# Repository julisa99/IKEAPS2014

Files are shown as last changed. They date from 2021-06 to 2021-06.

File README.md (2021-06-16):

# IKEAPS2014
Control your IKEA PS 2014 lamp with a servo motor and Wemos d1 mini (ESP8266) via Alexa – dimmable solution 💡

The year is 2021 and I finally managed to put my Ikea hack online. Of course, there are already countless hacks to be found on the internet. The special thing about this tutorial is that I set myself a goal: easy to replicate, easily replaceable and most importantly, the lamp not only just opens and closes; It is dimmable! You can open the lamp for example 20% or 80% via Alexa.
In the end, I only use the ESP8266 and a servo with an encoder, but more details will follow after the short animation of the working lamp:
<p align="center">

</p>

## Materials
1. [1x IKEA PS 2014 lamp](https://www.ikea.com/de/de/p/ikea-ps-2014-haengeleuchte-weiss-silberfarben-90311494/)
2. [1x WeMos D1 Mini](https://www.amazon.de/dp/B01N9RXGHY)
3. [1x Micro USB cable](https://www.amazon.de/dp/B01A9GLG6Q/)
4. [1x Feetech FB5317M 360° Servo - includes Analog Feedback with Magnetic Encoder](https://www.premium-modellbau.de/feetech-fb5317m-3600-cont-digital-servo-65g-17-5kg-feedback-arduino)
5. [1x servo mount](https://www.amazon.de/dp/B07SGPBCHM)
6. [1x sewing thread spool](https://www.amazon.de/dp/B074HF2KZV/)
7. [1x power supply 5V](https://www.amazon.de/dp/B00MWQD43U/)
8. [2x Wago connection clamp 3 x 0,2-4mm²](https://www.amazon.de/dp/B071ZHC2QH)
9. [2x 10cm braids 1,5mm² thickness for 230V](https://www.amazon.de/dp/B077JZNWV7)
10. [2x jumper cable male](https://www.amazon.de/dp/B01EV70C78/)
11. [1x 30cm 4-wire white cable or 8-wire flat ribbon telephone cable for extension from motor to ceiling](https://www.amazon.de/dp/B07TGKPFHK/)
12. [7x white cable ties](https://www.amazon.de/dp/B07JMKK66N)
13. [Optional: Crimping tool for cable lugs](https://www.amazon.de/gp/product/B07QMHNKW3)
14. [Optional: Crimping tool Dupont Set](https://www.amazon.de/dp/B078K9DT69/)
15. 3D printer for [servoHolder.stl](https://github.com/julisa99/IKEAPS2014/blob/main/servoHolder.stl)

## Preparation
Remove the white plastic spool from the frame of the lamp (see graphic) and cut the cord so that one side of the cord is longer than the other. We will knot the longer side to the sewing thread spool later. You can make the shorter side even shorter, because one cord with ball will be decoration.
<p align="center">

</p>

## Composition
Be careful, check that you have turned off the fuses of your power supply, otherwise you might severely hurt yourself. I know that even without being an electrician ;)
<p align="center">

</p>

As you can see in the graphic, the wiring is not complicated. The orange Wago clamps and the cable lugs provided an easy and comfortable way to set everything up. But now follows a little explanation:

The servo motor has four cables. The orange one (analog feedback) you plug into A0 of the Wemos. The white data cable you plug into D0. I don't supply the power for motor via the microcontroller, because it only gives up to 500mA via the pins, but the motor could overload this, by drawing up to 1800mA when it turns. The power for the motor and microcontroller comes from the power supply, which outputs 5V. To make the four cables fit to the 2 connectors, I feed + and - through each of the Wago clamps and put a jumper cable in there. Then I screwed the respective jumper cables (red: + and black: -) to the power supply by replacing the end with cable lugs.
I then connected the yellow ground cable from the ceiling to the ground of the power supply. Finally I attached cable lugs to two 10cm cables (with 1,5mm² thickness because of the higher current) to attach them at N and L between the power supply and the lamp as shown in the graphic with the brown and blue cable.

I later placed the servo motor in the lamp and put everything else up in the tray on the ceiling. Since the four cables from the motor are too short to reach from the ceiling to the center of the lamp, I used a white flat telephone cable and connected that as a 30cm extension to the cable ends from the motor and then the other end of the telephone cable into the microcontroller/Wago clamps. My telephone cable had 8 wires, where I then attached Dupont connectors myself, so that always 2 wires were together and I thus had 4. Alternatively you can use a 4-wire cable. (I got it as a drum of 100 meters of telephone cables, whose remains I still need to find some good use for. If you are from Germany near Berlin I can give you some :D)

<p align="center">



</p>

That's all for the cabling. Now only the attachment of the sewing thread spool to the motor and then the attachment of the motor in the lamp is missing.
I screwed the sewing thread spool to the black circular servo horn with two small screws and then screwed the servo horn to the motor.
<p align="center">

</p>

I then screwed the motor to the aluminum servo holder I bought and then made my own 3D model [servoHolder.stl](https://github.com/julisa99/IKEAPS2014/blob/main/servoHolder.stl) where I screwed the servo holder to it. My 3D model consists of a rod with two slots at the ends, where a cable tie is attached, which then holds on the frame of the lamp. This makes it easy to remove the motor at any time. 
<p align="center">

</p>

Afterwards you attach the white cord of the lamp to the metal sewing thread spool with a knot. With further cable ties you can lead your cable along the frame up to the ceiling. The assembly is finished!

<p align="center">

</p>

## Arduino IDE and library
In order to control the ESP8266, the following address must be added in the Arduino IDE under `File->Preferences->Additional Board Manager URLs`: http://arduino.esp8266.com/stable/package_esp8266com_index.json. Then you can type "esp8266" in the search field under `Tools->Board->Boards Manager`and click on `Install`. Now the `LOLIN(WEMOS) D1 R1 & mini` appears under the boards and can be selected.

For communication with Alexa I use the library "espalexa" with version 2.4.7. There is a small bug, which is fixed, if in line 197 in Espalexa.h `arg(0)` is changed to `argName(0)`.

In line 5 and 6 of [IKEAPS2014.ino](https://github.com/julisa99/IKEAPS2014/blob/main/IKEAPS2014.ino) you have to enter your access data for your wifi. After that you can upload the code to your microcontroller. In the end you can ask Alexa to search for new devices and you should find the device "star".

## How it works
When you command "Alexa, open star to 20%"; the function `deviceChanged(brightness)` is executed, where the 20% is passed as `brightness` of "51", since brightness value is between 0-255.
Now I calculate how often the sewing thread spool has to rotate. I have set `MAX_ROTATION` to how many times my cord must be wound on the sewing thread spool until the lamp is fully open. In my case, `MAX_ROTATION` is 4500, which would be ~4.4 revolutions (=4500/1024). This is because the encoder of the motor provides values of 0-1024 for the rotation range of 0°-360°. So I calculate 20% of 4500 (=900) as target of the motor. 

Now I decide in which direction the motor has to rotate to achieve the target position. Because the encoder is sometimes a bit inaccurate, I use an offset for the target position, which can be adjusted arbitrarily. If the 20% is not reached, the lamp will either move open or close until the 20% is reached (depending on the last position; at 0% it would now opens to reach 20%).
Here the function `onRotate(direction)` is used. This counts how many rounds the sewing thread spool has been rotated. Whenever the value of `FEEDBACK_PIN` changes between 1024 and 0, a round is done. Therefore I calculate the difference between the last position value and the current one. Since the encoder is imprecise, I don't check for exactly 1024 but only if the amount of the difference is greater than 500. I stop spinning the sewing thread spool as soon as the correct number of rounds and degrees is reached.

That's it, so the lamp can be moved dimmable.

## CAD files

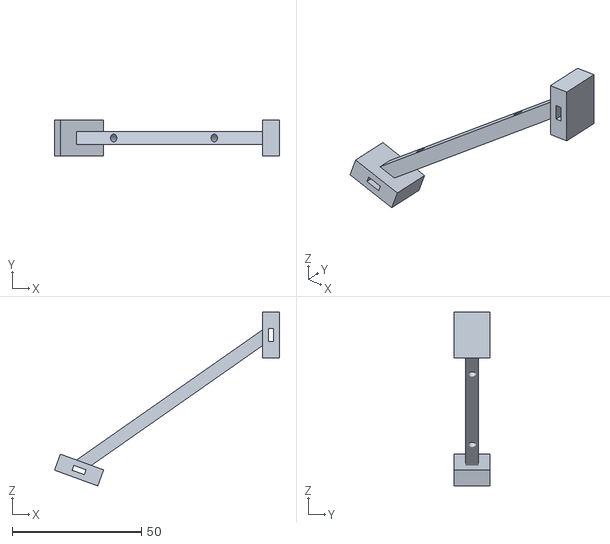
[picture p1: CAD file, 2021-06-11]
servoHolder.stl
87.0 x 14.0 x 67.2

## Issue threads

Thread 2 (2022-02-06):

How to attach white lamp cord to the sewing thread spool

krulkip, 2022-02-06:
What a lovely design. Thank you.
Do you simply tie the cord to one of the holes in the sewing thread spool.
I am combining it with: https://www.instructables.com/IKEA-PS-2014-Death-Star-Lamp/
And then controlling both the lamp and opening though Alexa.

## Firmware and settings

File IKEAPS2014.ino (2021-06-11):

#include <ESP8266WiFi.h>
#include <Espalexa.h> // https://github.com/Aircoookie/Espalexa/issues/6 needs to change in line 197 in Espalexa.h 'arg(0)' to 'argName(0)'
#include <Servo.h>

static constexpr char* WIFI_SSID = "your-ssid";
static constexpr char* WIFI_PASS = "your-password";

static constexpr int SERVO_PIN = 16;    // 2 from D4 | 16 from D0
static constexpr int FEEDBACK_PIN = A0; // A0 from Magnetic Encoder

static constexpr int FEEDBACK_OFFSET = 50; // select the value until you have outsmarted your unprecise encoder
static constexpr int MAX_FEEDBACK = 1024;
static constexpr int MAX_ROTATION = 4500;
static constexpr int MAX_TURN = MAX_ROTATION / MAX_FEEDBACK;

Servo servoMotor;
Espalexa espalexa;

uint8_t oldBrightness = 0;
int currentTurn = 0;
int targetTurn = 0;
int targetPos = 0;
int pos = 0;
int oldPos = 0;

enum class Direction : int {
  forward = 1,
  backward = -1
};

void wifiSetup() {
  WiFi.mode(WIFI_STA);
  WiFi.begin(WIFI_SSID, WIFI_PASS);
  while (WiFi.status() != WL_CONNECTED) {
    delay(100);
  }
}

bool isInRange(int lower, int upper, int current) {
  return lower <= current && current <= upper;
}

// check target position with offset (accurancy problem of encoder)
bool isTargetPosWithOffset(int current, int target) {
  int lower = (target + MAX_FEEDBACK - FEEDBACK_OFFSET) % MAX_FEEDBACK;
  int upper = (target + FEEDBACK_OFFSET) % MAX_FEEDBACK;
  if (lower > upper) {
    return isInRange(lower, MAX_FEEDBACK, current) || isInRange(0, upper, current);
  } else {
    return isInRange(lower, upper, current);
  }
}

void onRotate(const Direction direction) {
  while (currentTurn != targetTurn || !isTargetPosWithOffset(pos, targetPos)) {
    yield();
    if (direction == Direction::forward && currentTurn > MAX_TURN) {
      return startRotate();
    } else if (direction == Direction::backward && currentTurn < 0) {
      return startRotate();
    }
    pos = analogRead(FEEDBACK_PIN);
    if (abs(oldPos - pos) > 500) {
      currentTurn += static_cast<int>(direction);
    }
    oldPos = pos;
  }
}

void startRotate() {
  if (currentTurn * MAX_FEEDBACK + pos < targetTurn * MAX_FEEDBACK + targetPos) {
    servoMotor.writeMicroseconds(2000); // when high level is 1.5~2ms, servo rotates counter clockwise
    onRotate(Direction::forward); // open lamp
  } else {
    servoMotor.writeMicroseconds(1000); // when high level is 1~1.5ms, servo rotates clockwise
    onRotate(Direction::backward); // close lamp
  }
}

void deviceChanged(uint8_t brightness) { // brightness value between 0-255
  if (oldBrightness == brightness) {
    return;
  }
  oldBrightness = brightness;
  int targetRotation = static_cast<int>(MAX_ROTATION * (static_cast<float>(brightness) / 255.f));
  targetTurn = targetRotation / MAX_FEEDBACK;
  targetPos = targetRotation % MAX_FEEDBACK;
  pos = analogRead(FEEDBACK_PIN);
  oldPos = pos;

  servoMotor.attach(SERVO_PIN);
  startRotate();
  servoMotor.writeMicroseconds(1500); // servo will stop rotating when reaching 1.5ms
  servoMotor.detach();
}

void setup() {
  pinMode(FEEDBACK_PIN, INPUT);
  wifiSetup();
  espalexa.addDevice("star", deviceChanged);
  espalexa.begin();
}

void loop() {
  espalexa.loop();
  delay(1);
}
